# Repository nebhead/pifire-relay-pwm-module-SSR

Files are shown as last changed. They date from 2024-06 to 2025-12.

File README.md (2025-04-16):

# PiFire Solid State Relay (SSR) Module PCB (v1.0.1) KiCad Files

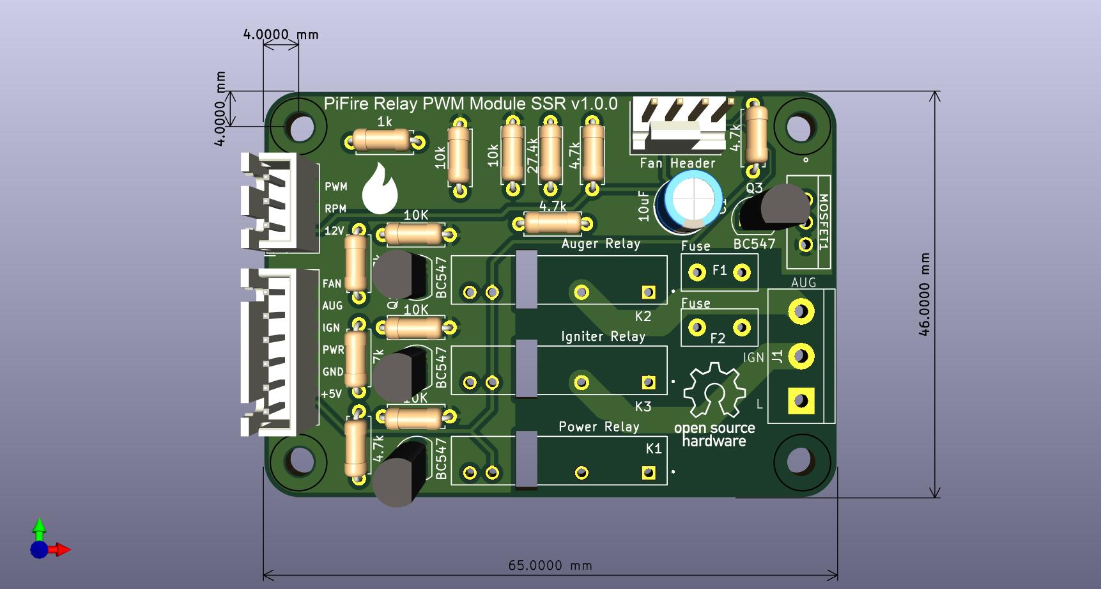
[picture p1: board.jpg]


## What is this? 

This PCB is designed to support SSR relays for controlling incoming Power(L) to the Igniter and Auger.  This board also has circuitry to support a 12V PWM fan.  This board uses compact solid state relays that are able to handle high power. This is an alternative to using an off the shelf relay module which simplifies the wiring and even allows you to use the OEM harness.  

The design intent for this board was to make a DIY accessible PCB that can be more easily put together by the maker/enthusiast of almost any skill level.  Full size components are used in most cases and most (if not all) parts should be readily available to order online.  See the [Interactive BOM](#interactive-bom) for more details about the parts used and links to order.

### Important Notes

This PCB is intended to be used with the 4.0.x PCB design ([linked below](#links-to-the-pcbs-in-this-family-of-pifire-boards)) in conjunction with v1.8.x or later of the PiFire software.

The G3MB Relays and the PSMN MOSFET footprints have been left out of this release because they were sourced from SnapMagic (for free), but are not licensed for re-distribution.  If you plan to edit this board, you may need to source those files from SnapMagic directly and add them to this project.  

### What is PiFire? 

PiFire is a SBC based Pellet Smoker Controller.  More details can be found [here](https://nebhead.github.io/PiFire) or [at the GitHub repo](https://github.com/nebhead/pifire). 

## What's in this Repository?

### KiCad Project Files 
In this repository you will find the latest KiCad design files for the  PCB.  Simply load the project file (.kicad_pro) into the KiCad software and you should be able to edit as needed.  Or if you just want to get this board made, jump to the production section below.

### Interactive BOM

There is an interactive BOM located in the [/bom](bom/) folder which details the parts and provides some pin information as well.  Use this to gather the components you may need to build this board out and refer back to it for placement help.    

[BOM + Pin Info](https://nebhead.github.io/pifire-relay-pwm-module-SSR)

_This is a standalone HTML file that was autogenerated by the excellent plugin for KiCad. See the plugin here: [https://github.com/openscopeproject/InteractiveHtmlBom](https://github.com/openscopeproject/InteractiveHtmlBom)_

### PDF of the Schematic

Preview the schematic in PDF format here: [Schematic](schematic.pdf)

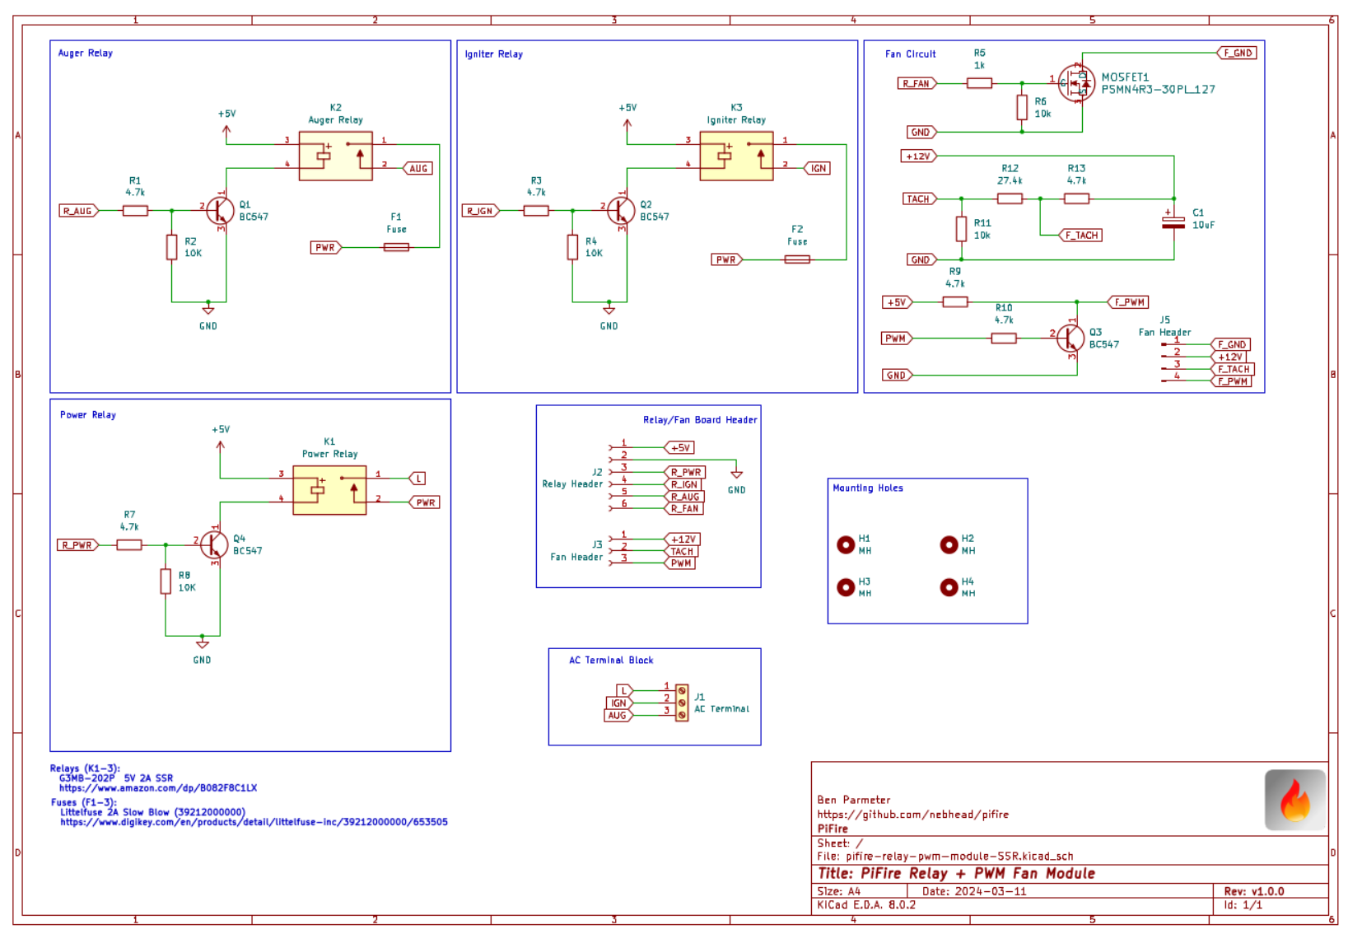
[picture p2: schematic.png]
Schematic PNG


### PWM Fan Pinout

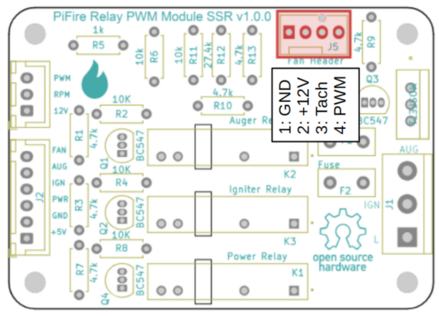
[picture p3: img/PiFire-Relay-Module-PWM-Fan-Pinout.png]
PWM Fan Pinout


The PWM fan pinout is using a standard 4-pin fan connector.  It's recommended to source the headers with retaining clip to ensure that the fan doesn't easily come unplugged.  JST headers can be used as well. 

### JLCPCB Production Files

If you wish to get these PCBs made by JLCPCB, the production files are provided in the `/production` folder.  For convenience, the file `production.zip` can simply be uploaded to JLCPCB to make it super easy to order boards.

Drop the zip file onto the order page, wait for it to upload then simply continue to order the board.  Optionally, select different board color, PCB quantity, surface finish, etc.  Most of the default settings should be sufficient. 

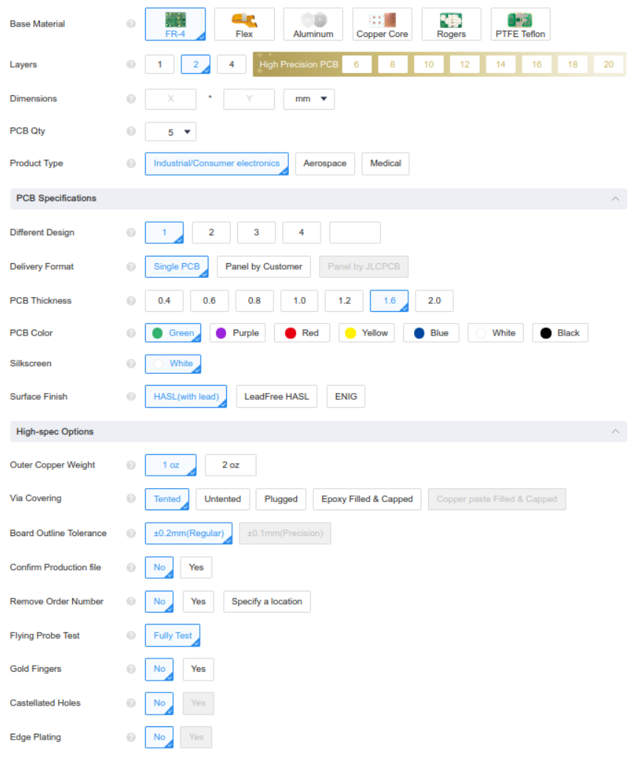
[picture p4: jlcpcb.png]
JLCPCB Order Page


### Links to the PCBs in this family of PiFire Boards

This PCB is part of a family of PCBs that can be used together to create  a full PiFire system.  Generally speaking you need the Main Module/Board, a Relay Control Board and a Probe Device board to have a basic PiFire system.  

**Main Module/Board** (required)
* [Main Board v4.0.x](https://github.com/nebhead/pifire-main-module-nopwr)

**Relay/Fan Control Boards** (choose one)
* [Mechanical Relay Module](https://github.com/nebhead/pifire-relay-module)
* [Solid State Relay Module](https://github.com/nebhead/pifire-relay-module-ssr)
* [Solid State Relay + PWM Fan Module](https://github.com/nebhead/pifire-relay-pwm-module-ssr) - Original Design
* [Solid State Relay + PWM Fan Module Alternate](https://github.com/nebhead/pifire-relay-pwm-module-ssr-alt) - Updated Design (Designed with help from @labmonkeyrat on Discord)

**Probe Device Board** (optional)
* [ADS Board](https://github.com/nebhead/pifire-ads-board) 

### 3D Printable Enclosures/Boxes 

With all of the 3D Prints for PiFire, a higher temperature filament such as PETG should be used.  PLA generally won't stand up to the temperatures that the components may be exposed to outdoors and near a hot smoker.  

#### Enclosure

Included here is an initial revision of the enclosure for this PCB.  The current models should be considered still in development and may have alignment challenges, etc. 

Except for the mounting wings, the majority of bolts to be used with this enclosure are M3. 

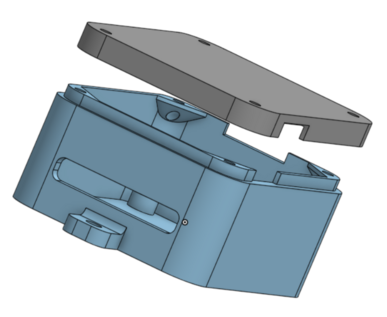
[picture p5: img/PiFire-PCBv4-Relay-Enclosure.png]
Enclosure


* STL: [Base](/printables/PiFire-v4-Relay-Base.stl)
* STL: [Lid](/printables/PiFire-v4-Relay-Lid.stl)
* OnShape: [Enclosure Original Models](https://cad.onshape.com/documents/03559f76f7adf190bf6f1259/w/7529cb0e4cd69db1a6a15202/e/07d5f9d46dc8f2b9e7dd655f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)

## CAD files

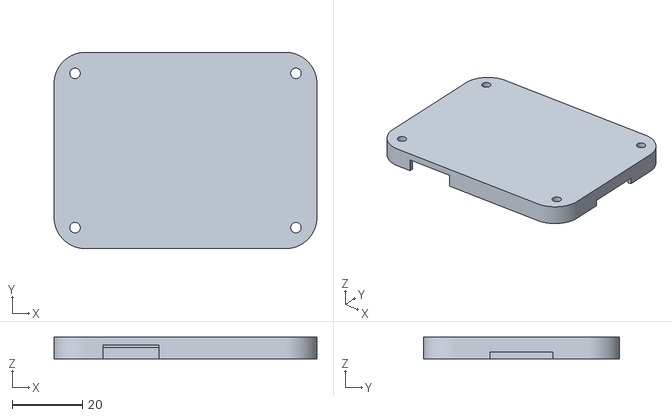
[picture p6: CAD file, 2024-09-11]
printables/PiFire-v4-Relay-Lid.stl
75.0 x 56.0 x 6.20

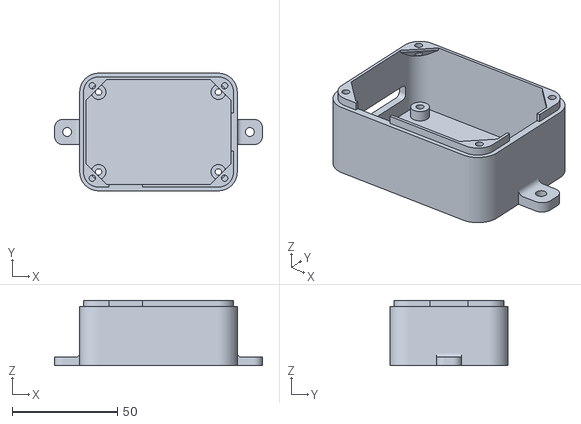
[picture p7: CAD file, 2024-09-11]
printables/PiFire-v4-Relay-Base.stl
99.0 x 56.0 x 31.0

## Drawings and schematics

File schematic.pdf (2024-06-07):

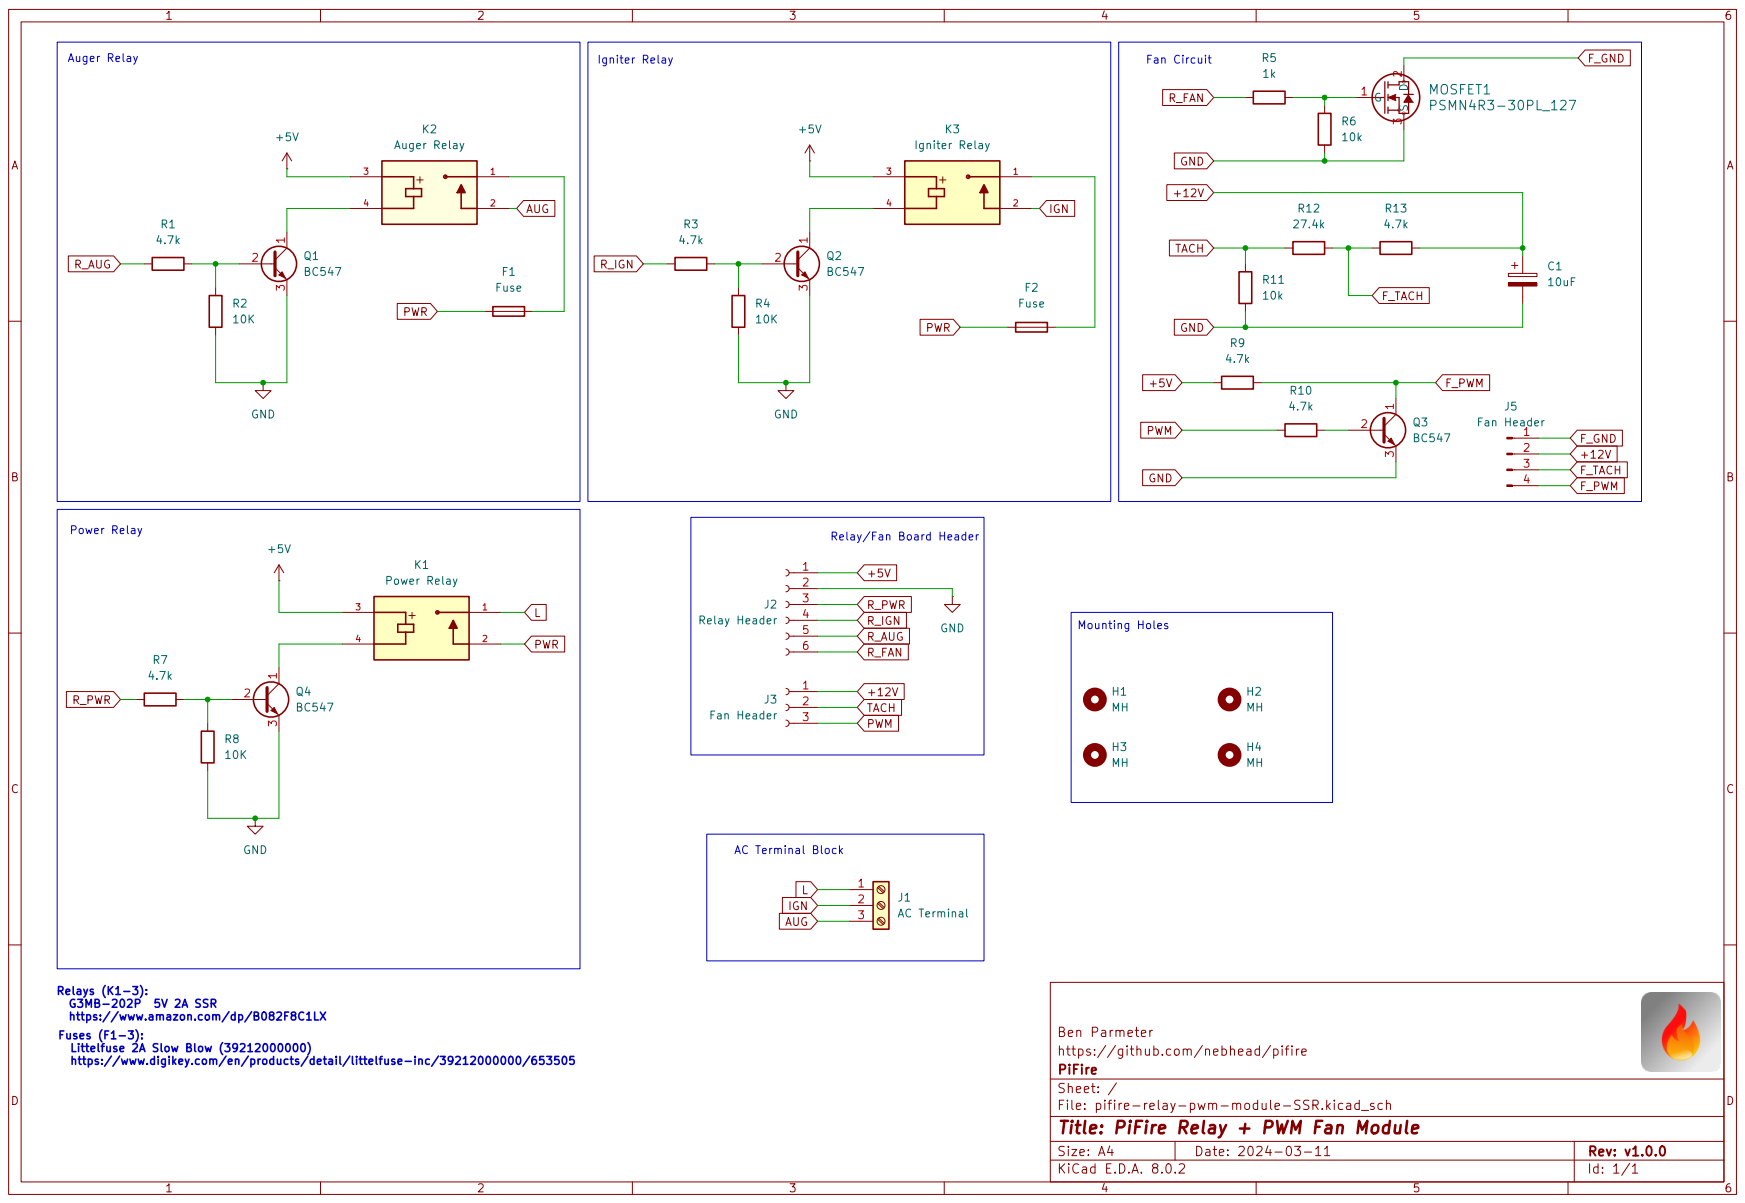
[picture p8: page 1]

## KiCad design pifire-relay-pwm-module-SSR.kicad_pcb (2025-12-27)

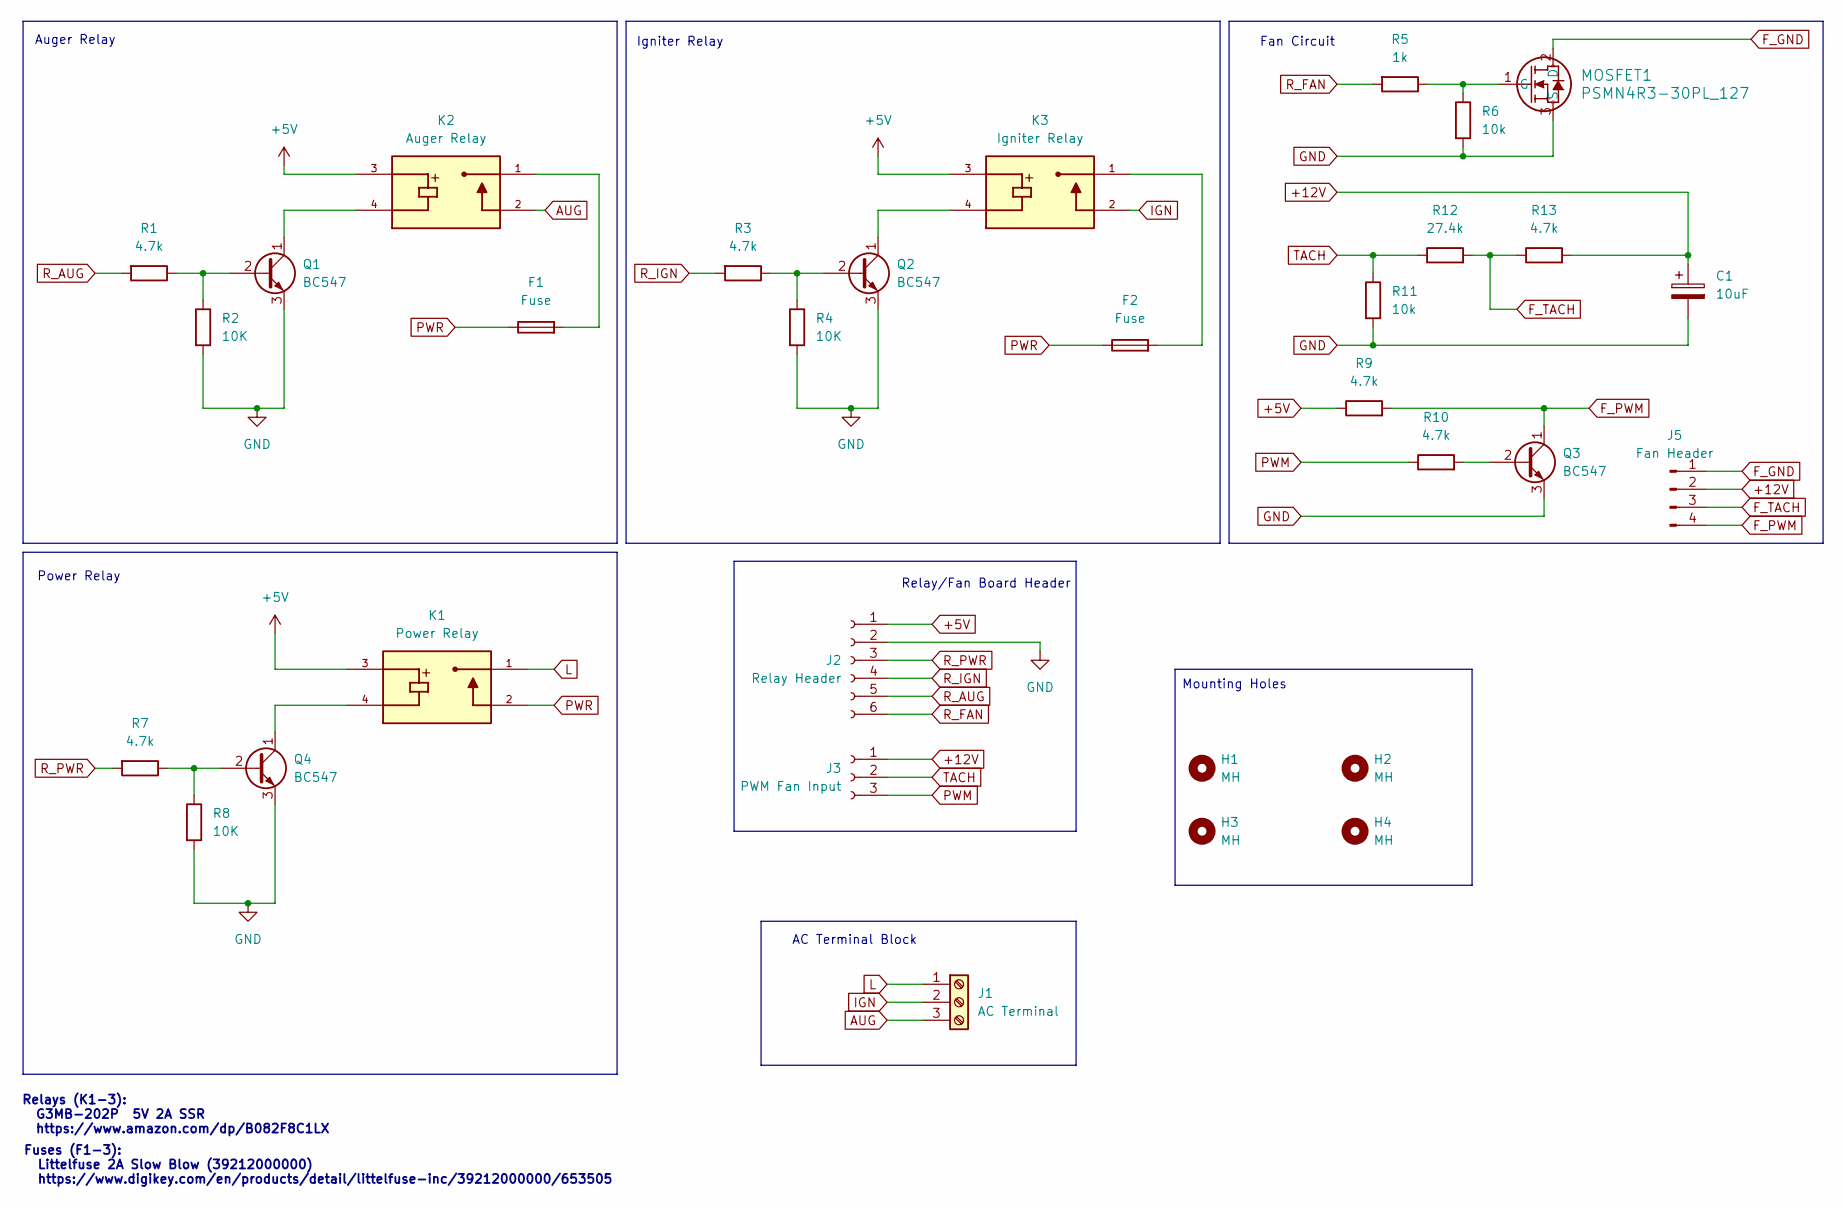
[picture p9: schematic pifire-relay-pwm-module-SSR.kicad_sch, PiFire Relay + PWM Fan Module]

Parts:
C1: 10uF; CP_Radial_D6.3mm_P2.50mm
F1, F2: Fuse; Fuse_Littelfuse_395Series
H1, H2, H3, H4: MH; MountingHole_3.2mm_M3
J1: AC Terminal; TerminalBlock_bornier-3_P5.08mm
J2: Relay Header; JST_XH_B6B-XH-A_1x06_P2.50mm_Vertical
J3: PWM Fan Input; JST_XH_B3B-XH-A_1x03_P2.50mm_Vertical
J5: Fan Header; FanPinHeader_1x04_P2.54mm_Vertical
K1: Power Relay; RELAY_G3MB-202PDC5; PARTREV J091-E1-1A
K2: Auger Relay; RELAY_G3MB-202PDC5; PARTREV J091-E1-1A
K3: Igniter Relay; RELAY_G3MB-202PDC5; PARTREV J091-E1-1A
MOSFET1: PSMN4R3-30PL_127; TO-220AB_SOT78_NEX
Q1, Q2, Q3, Q4: BC547; TO-92L_Inline
R1, R3, R7, R9, R10, R13: 4.7k; R_Axial_DIN0207_L6.3mm_D2.5mm_P7.62mm_Horizontal
R2, R4, R8: 10K; R_Axial_DIN0207_L6.3mm_D2.5mm_P7.62mm_Horizontal
R5: 1k; R_Axial_DIN0207_L6.3mm_D2.5mm_P7.62mm_Horizontal
R6, R11: 10k; R_Axial_DIN0207_L6.3mm_D2.5mm_P7.62mm_Horizontal
R12: 27.4k; R_Axial_DIN0207_L6.3mm_D2.5mm_P7.62mm_Horizontal

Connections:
+5V: J2.1, K1.3, K2.3, K3.3, R9.1
+12V: C1.1, J3.1, J5.2, R13.2
AUG: J1.3, K2.2
F_GND: J5.1, MOSFET1.2 (D)
F_PWM: J5.4, Q3.1 (C), R9.2
F_TACH: J5.3, R12.2, R13.1
GND: C1.2, J2.2, MOSFET1.3 (S), Q1.3 (E), Q2.3 (E), Q3.3 (E), Q4.3 (E), R2.2, R4.2, R6.2, R8.2, R11.2
IGN: J1.2, K3.2
L: J1.1, K1.1
unnamed: F1.2, K2.1
unnamed: F2.2, K3.1
unnamed: MOSFET1.1 (G), R5.1, R6.1
unnamed: Q1.2 (B), R1.1, R2.1
unnamed: K2.4, Q1.1 (C)
unnamed: Q2.2 (B), R3.1, R4.1
unnamed: K3.4, Q2.1 (C)
unnamed: Q3.2 (B), R10.2
unnamed: Q4.2 (B), R7.1, R8.1
unnamed: K1.4, Q4.1 (C)
PWM: J3.3, R10.1
PWR: F1.1, F2.1, K1.2
R_AUG: J2.5, R1.2
R_FAN: J2.6, R5.2
R_IGN: J2.4, R3.2
R_PWR: J2.3, R7.2
TACH: J3.2, R11.1, R12.1

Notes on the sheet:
Fan Circuit
Power Relay
Fuses (F1-3): Littelfuse 2A Slow Blow (39212000000) https://www.digikey.com/en/products/detail/littelfuse-inc/39212000000/653505
AC Terminal Block
Auger Relay
Relay/Fan Board Header
Relays (K1-3): G3MB-202P 5V 2A SSR https://www.amazon.com/dp/B082F8C1LX
Mounting Holes
Igniter Relay

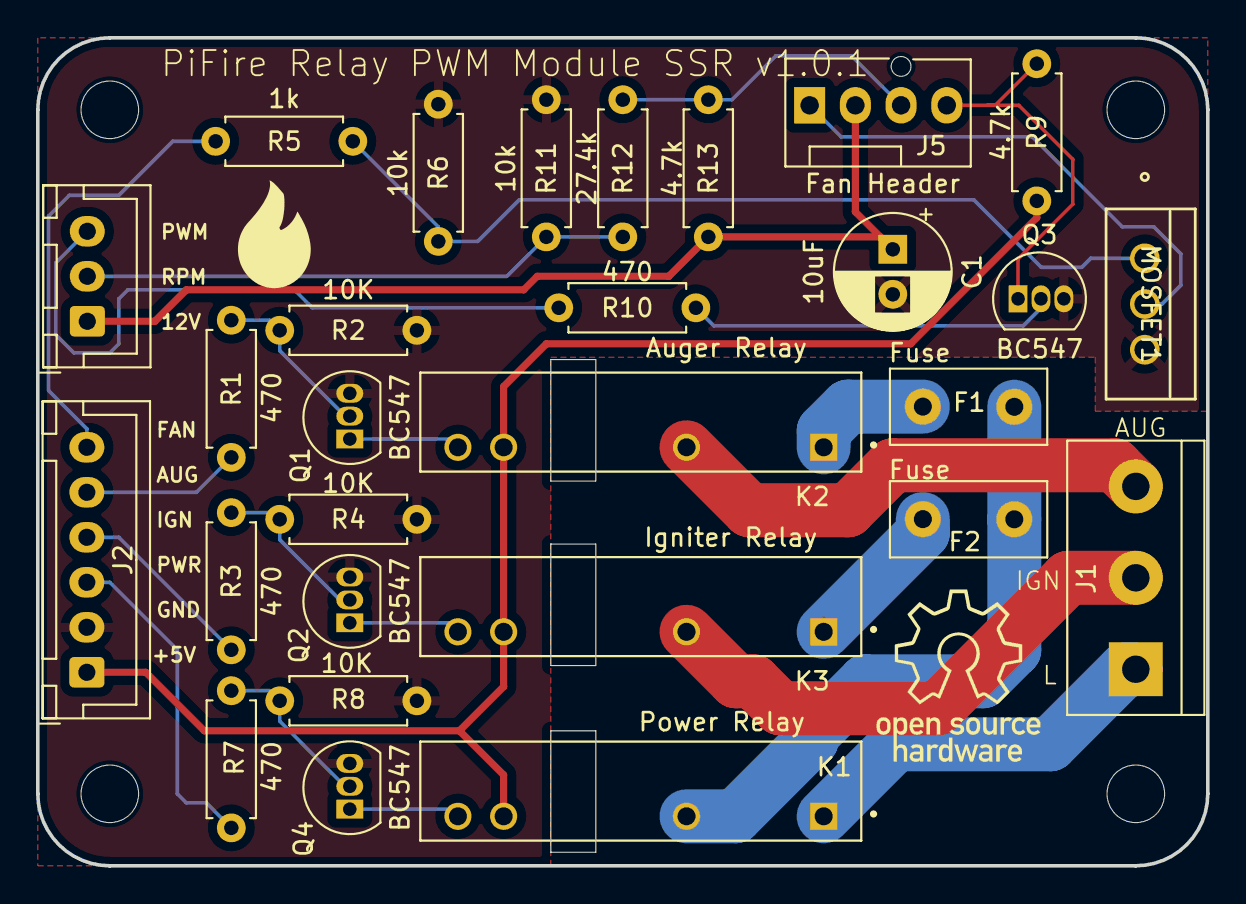
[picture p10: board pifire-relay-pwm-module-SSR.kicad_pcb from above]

Board: 2 copper layers, 65.0 x 46.0 mm, 32 parts (0 on the bottom side), 26 nets.

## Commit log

2024-06-07 First Release
    [pifire-relay-pwm-module-SSR-B_Cu.gbl, pifire-relay-pwm-module-SSR-B_Mask.gbs, pifire-relay-pwm-module-SSR-B_Paste.gbp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]
2024-06-07 Update link to BOM
2024-06-07 Rename BOM HTML
2024-09-07 Update README.md
    Add alternate PWM board.
2024-09-11 Added 3D Printables
    [PiFire-v4-Relay-Base.stl, PiFire-v4-Relay-Lid.stl]
2025-04-16 Updated with PWM Fan Pinout
2025-12-27 Update to v1.0.1
    [pifire-relay-pwm-module-SSR-B_Cu.gbl, pifire-relay-pwm-module-SSR-B_Mask.gbs, pifire-relay-pwm-module-SSR-B_Paste.gbp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]
2025-12-27 Updated Schematic
    [pifire-relay-pwm-module-SSR.kicad_sch]
